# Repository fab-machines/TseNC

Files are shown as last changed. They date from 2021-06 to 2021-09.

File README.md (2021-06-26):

<div align="center"><h1 style=align="center">TseNC</h1></div>

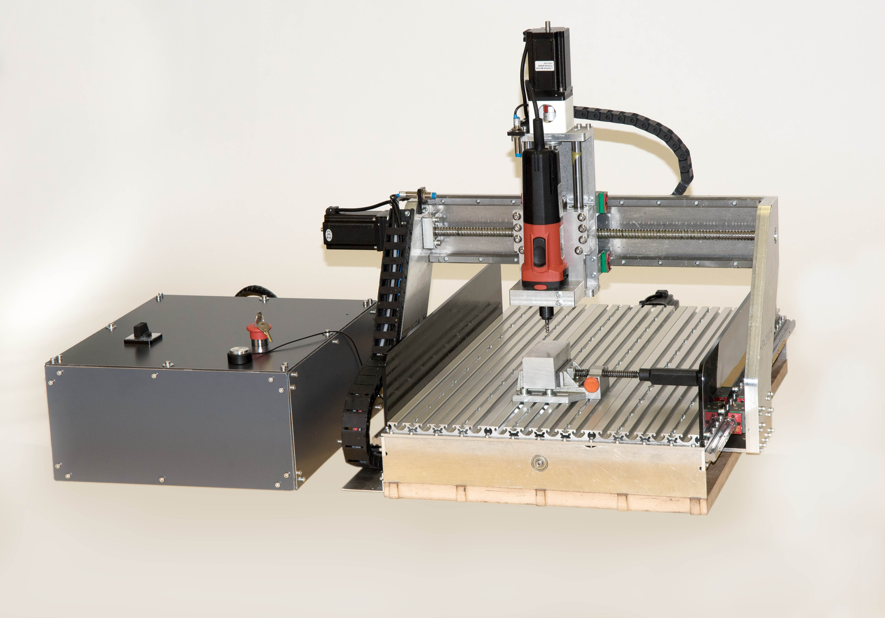
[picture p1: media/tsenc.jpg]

<div align="center"><i>Open Source CNC Milling Machine</i></div>

TseNC specifications
--

- working area: 600x370x145mm Y-X-Z (400mm on X with no side protection)
- frame: solid aluminum plates of 6/8/12/20mm bolted
- Bed: aluminum nut profiled Nut 8
- actuators: 16mm ballscrews on X and Y, 12mm ballscrew on Z
- linear guides: Hiwin HGR15
- maximum speed: 4000mm/min
- mechanical resolution: 0.003125mm
- spindle: Mafell FM1000 1Kw
- firmware: GRBL-LPC
- controller: LPC1768 32bit
- motors: NEMA 24 4MN
- motor controllers: 3 x DM556
- compatible collets: 3/4/5/6/8mm 1/8 and 1/4
- quick spindle release
- Z zero sensor
- inductive endstops with softlimits
- side procection of 6mm POM
- emergency button with fuse protection

Author
--
Project Lead:<br>
Prof. Dr. William Megill<br>
Prof. Dr. Karsten Nebe
<br>
<br>
Machine design and fabrication:<br>
Daniele Ingrassia
<br>
<br>
Technical help and assembly:<br>
Leen Nijim<br>
Kevin Brinkmann<br>
<br>
Rhine-Waal University of Applied Sciences<br>
https://www.hochschule-rhein-waal.de/en

License
--

TseNC and all the work in this repository is released under the following open source license:

CERN Open Hardware Licence - Weakly Reciprocal, CERN-OHL-W

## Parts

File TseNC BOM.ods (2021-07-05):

Name | Specifications | Amount | Unit Price (inkl. Mwst) | Total | Shipping | Vendor | Unique Vendor | Status | William | Daniele | Invoice Amt | Invoice No | Location | Total:
Linear Bearing Block | HGH15CA | 7 | €33.00 | €231.01 | 4.88 € | link (https://www.cnc-zubehoer.eu/antriebe/profilschienenfuehrungen/201/hiwin-laufwagen-hgh?c=121) | cnc-zubehoer (<=200€ netto) | Arrived | reimbursement claimed |  | €235.90 |  | Xanten (verified) | €1,793.33
Linear Bearing Block | HGH15CA | 1 | €25.00 | €25.01 |  | link (https://www.cnc-store.eu/en/bearings-blocks/bearing-block-hgh15cazac.html) | cnc-store(<=200€ netto) | Arrived | reimbursement claimed |  | €188.31 |  | Xanten (verified)
Linear Rail | HGR15RC 800mm | 2 | €40.80 | €81.98 | 8.11 € | link (https://www.cnc-store.eu/en/linear-guideways-126/guideway-hgr15-r-c.html) |  |  |  |  |  |  |  | Total netto:
Linear Rail | HGR15RC 500mm | 2 | €25.50 | €51.24 | 21.96 € |  |  |  |  |  |  |  |  | €1,545.98
Linear Bearing | LME16UU | 4 | €6.30 | €25.20 |  | link (https://www.dold-mechatronik.de/Linear-bearing-16mm-LME16UU) | dold-mechatronik (<=200€ netto) | Arrived | rechnung paid in mach |  | €224.50 | 71089 | Xanten (verified)
Linear shaft | 16mm H6 350mm | 4 | €5.10 | €20.40 |  | link (https://www.dold-mechatronik.de/Precision-shaft-16mm-h6-honed-and-hardened-300mm)
Ball Screw | 1610 800mm including nut | 1 | €90.00 | €90.00 |  | link (https://www.dold-mechatronik.de/Ball-screw-SFU1610-3-800mm)
Ball Screw | 1610 600mm including nut | 1 | €82.00 | €82.00 | 6.90 € | link (https://www.dold-mechatronik.de/Ball-screw-SFU1610-3-600mm)
Ball Screw | 1605 300mm including nut | 1 | €35.79 | €35.79 |  | link (https://gtech-shop.de/Kugelumlaufspindel-SFU1605-300mm) | GTech (<=200€ netto) |  | did this get ordered? |  |  |  |  | Missing
Coupler | D25L30 8mm to 10mm | 6 | €6.50 | €34.69 |  | link (https://gtech-shop.de/Wellenkupplung-Aluminium-flexibel-D25L30-8mm) |  | Arrived | reimbursement claimed, but needs to be switched to correct Kostenstelle |  | €101.12 |  | Xanten (verified) | They are 8 to 8mm not 8 to 10mm
Bearing | 6000ZZ | 16 | €0.80 | €10.76 |  | link (https://gtech-shop.de/Rillenkugellager-6000-ZZ) |  |  |  |  |  |  |  | cable chain are only 2
Cable Chain | Open/Closed 25x57 | 1 | €18.29 | €18.29
Cable Chain | Open/Closed 25x25 | 1 | €17.49 | €17.49 |  | link (https://gtech-shop.de/Offen-25-x-38)
Cable Chain | 30mm | 2 | €1.99 | €3.98
Cable Chain | 30mm VPE | 1 | €3.49 | €3.49
Cable Wrapper | 20mm | 2 | €1.49 | €2.98 |  | link (https://gtech-shop.de/Kabelfuehrung-Kabelbuendel-Schwarz-R20mm-25m-1-Meter)
Cable Wrapper | 10mm | 5 | €1.10 | €5.45 | 3.99 €
Aluminum Plate | 300x300x25mm CNC friendly (AlMg3, AlMgSi1 or similar) | 1 | €75.60 | €75.60 |  | link (https://www.duerr-metall.shop/p/aluminium-gussplatten-25mm-dicke-almg3-300x300mm) | DURR (<=200€ netto) | Arrived | Rechnung paid in mach |  | €189.00 | 1098 | Xanten (verified)
Aluminum Stock | 50x50x150mm CNC friendly (AlMg3, AlMgSi1 or similar) | 8 | €13.30 | €106.40 | 7.00 € | link (https://www.duerr-metall.shop/p/aluminium-vierkant-50x50mm-almgsi1-100mm)
Aluminum Plate | 800x750x6mm | 1 | €91.00 | €90.99 |  | link (https://www.ebay.de/itm/6-10mm-Aluminium-Blech-Platte-Alublech-Aluplatte-Feinblech-Zuschnitt-wahlbar/263589302349) | HLS tactical (<=200€ netto) | Arrived | reimbursement claimed |  | €90.99 |  | Xanten (verified)
Stepper motor | Nema 24 4NM 8mm shaft | 3 | €34.30 | €102.90 | 64.07 € | link (https://www.omc-stepperonline.com/nema-24-stepper-motor/dual-shaft-nema-24-stepper-motor-42a-4nm-566-ozin-60x60x100mm-4-wires-24hs39-4204d.html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) | stepperonline (<=200€ netto) | Arrived | reimbursement claimed |  | €145.84 | 56759 | Xanten (verified)
Stepper Driver | TB6600 | 3 | €12.66 | €37.98 |  | link (https://www.mechatronics-pro.de/de/stepper-motor-treiber-tb6600-4a-9-42v-controller-steuerung-cnc-schrittmotor_618.html) | mechatronics pro (<=200€ netto) | Arrived | reimbursement claimed |  | €37.98 |  | Xanten (verified)
Spindle | Mafell FM 1000 | 1 | €230.84 | €230.84 |  | link (https://www.hbh24online.de/de/-31894.html) | HBH Baumaschinenhandel GmbH (<=200€ netto) | Arrived | reimbursement claimed |  | €230.84 |  | Xanten (verified) | Collets needed!
3D Printer Filament | PETG 1KG White 1.75mm | 2 | €13.95 | €27.91 | 4.90 € | link (https://www.igo3d.com/maertz-budget-petg-filament) | igo3D (<=200€ netto) | Arrived | reimbursement claimed |  | €32.80 | 388676 | Xanten (verified)
Flat Aluminum Profile | T-Nutenplatte 600x400 16(+)mm | 1 | €118.99 | €118.99 | 15.00 € | link (https://www.ebay.de/itm/T-Nutenplatte-aus-Aluminium-fur-High-Z-S-400-T-CNC-Portalfrasmaschine/372998543104) | cnc-step (<=200€ netto) | Arrived | reimbursement claimed |  | €133.99 | 2653 | Xanten (verified)
MDF Plate | 600x800x25(+)mm | 1 | €17.90 | €17.90 | 6.90 € | link (https://www.myspiegel.de/mdf-platten-pb-4244.html) | spiegel-shop (<=200€ netto) | Arrived | reimbursement claimed |  | €24.80 |  | Xanten (verified)
Dibond | 3mm 2050x1000mm White | 1 | 37.8 | €37.80 |  | link (https://onlineshop.firstbond.de/product_info.php?no_boost=1) | firstbond (<=200€ netto) |  | donated from ENSPIRE stock |  |  |  | Xanten (verified) | alternative: | 2 plates 500x500x3mm, 4 plates 400x500 | link (https://www.ebay.de/itm/47-99-m-DIBOND-Alu-Verbundplatte-weiss-matt-3-mm-Zuschnitt-Grose-wahlbar/362029668269)
Power Plug | Power Plug With Fuse and Switch | 1 | €3.19 | €3.19 | 2.20 € | link (https://www.ebay.de/itm/Kaltgerate-C14-Einbaustecker-250-V-10-A-Schalter-Sicherungshalter-Modul-14554/293009802941) | Inetbote.de e.K. (<=200€ netto) |  | reimbursement claimed |  | €5.39 | 70843 | Xanten (verified)
Aluminum Profile | 20x20 nut 6 450mm | 36 | €0.46 | €16.56 |  | link (https://www.alu-profil-technik.de/Profil20x20-Designprofil-Aluprofile-Strebenprofile-Solarpeofile-Alubaukasten.html) | alu-profil-technik (<=200€ netto) | Arrived | reimbursement claimed |  | €58.58 |  | Xanten (verified) | Seems wrong, but should be enough for what we need!
Aluminum profiles | 20x20 Nut 6 300mm | 12 | €0.46 | €5.52
Bracket | 20x20mm nut 6 | 15 | €2.05 | €30.75 | 5.75 € | link (https://www.alu-profil-technik.de/Winkel--Verbinder--Winkel-20.html)
Wire | LIYCY 4x0.5mm 1 meter | 10 | €1.06 | €10.60 | 6.90 € | link (https://www.ebay.de/itm/Steuerleitung-geschirmt-Datenleitung-LIYCY-2-12x0-14-1-5-mm-Schnittlange-lauf-M/283736151360) | powercables-shop (<=200€ netto) |  | reimbursement claimed |  | €37.60 |  | Xanten (verified)
Wire | LIYCY 3x0.25mm 1 meter | 10 | €1.01 | €10.10
Wire | 2x1.5mm 24V | 10 | €1.00 | €10.00 |  | link (https://www.ebay.de/itm/Niedervoltkabel-2x1-5-4-mm-Niedervoltleitung-max-24-V-SIF-PV-P-laufende-Meter/272840350273)
Emergency Button | Em. Button with key | 1 | €6.00 | €5.98 |  | link (https://www.ebay.de/itm/Notausschalter-Not-aus-Schalter-Druck-Notschalter-Auschalter-Druckschalter/281817794707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) | Katarzyna Klincewicz (<=200€ netto) | Arrived | reimbursement claimed |  | €18.88 |  | Xanten (verified)
Power Switch | Power Switch 20A 2 Polig 1 Phase | 1 | €8.00 | €7.98 | 4.92 € | link (https://www.ebay.de/itm/16-160A-Nockenschalter-Drehschalter-Wendeschalter-0-1-L-0-R-0-Y-1-0-2/282083342606)
AC Cable | PC AC Power Cable | 1 | €5.40 | €5.40 |  | link (https://www.ebay.de/itm/Stromkabel-PC-Netzkabel-Kaltgeratestecker-Computer-Monitor-Drucker-Top-Zustand/124164087445) | Tech-Ced e.k (<=200€ netto) | Arrived | reimbursement claimed |  | €5.40 | 196 | Xanten (verified)
Cable connector | 12 slots, 1.5-2.5mm 5 pieces | 1 | €5.95 | €5.95 |  | link (https://www.ebay.de/itm/Lusterklemmen-12-polig-Listerklemmen-Verbindungsklemmen-1-5-16mm-Lampen-Klemme/153006846657) | Dema-Trading, Matthias Dehs (<=200€ netto) | Arrived | reimbursement claimed |  | €5.95 | 69401 | Xanten (verified)
Magnetic Switches | PS-3150 | 10 | €2.29 | €22.89 |  | link (https://www.roboter-bausatz.de/2389/ps-3150-magnetschalter-no-schliesser) | roboter bausatz(<=200€ netto) |  | reimbursement claimed |  | €22.89 |  | Xanten (verified)
Nuts | DIN 985 M4 | 100 | €0.01 | €1.07 |  | link (https://malimo24.de/Sicherungsmuttern-DIN-985-galv-verzinkt-M4-100-Stueck) | QS Vertriebs (<=200€ netto) |  | reimbursement claimed |  | €53.92 |  | Xanten (verified)
Nuts | DIN 985 M5 | 100 | €0.01 | €1.07 |  | link (https://malimo24.de/Sicherungsmuttern-DIN-985-galv-verzinkt-M5-100-Stueck)
Nuts | DIN 985 M6 | 100 | €0.01 | €1.22 |  | link (https://www.ebay.de/itm/Sicherungsmuttern-Stopmuttern-Muttern-Din-985-verzinkt/150653102538)
Nuts | DIN 985 M8 | 100 | €0.02 | €2.44 |  | link (https://malimo24.de/Sicherungsmuttern-DIN-985-galv-verzinkt-M8-50-Stueck)
Screws | DIN 912 M4 20mm | 300 | €0.02 | €4.12 |  | link (https://www.ebay.de/itm/M4-MaLiMo-DIN-912-Zylinderschrauben-galv-verzinkt-8-8/311791183620)
Screws | DIN 912 M4 30mm | 200 | €0.03 | €4.35 |  | link (https://www.ebay.de/itm/M4-MaLiMo-DIN-912-Zylinderschrauben-galv-verzinkt-8-8/311791183620)
Screws | DIN 912 M5 10mm | 100 | €0.02 | €1.32 |  | link (https://www.ebay.de/itm/M5-MaLiMo-DIN-912-Zylinderschrauben-galv-verzinkt-8-8/381944072599)
Screws | DIN 912 M5 16mm | 100 | €0.02 | €3.18 |  | link (https://www.ebay.de/itm/M5-MaLiMo-DIN-912-Zylinderschrauben-galv-verzinkt-8-8/381944072599)
Screws | DIN 912 M5 22mm | 100 | €0.02 | €3.96 |  | link (https://www.ebay.de/itm/M5-MaLiMo-DIN-912-Zylinderschrauben-galv-verzinkt-8-8/381944072599)
Screws | DIN 912 M5 30mm | 100 | €0.03 | €4.55 |  | link (https://www.ebay.de/itm/M5-MaLiMo-DIN-912-Zylinderschrauben-galv-verzinkt-8-8/381944072599)
Screws | DIN 912 M6 10mm | 100 | €0.02 | €1.93 |  | link (https://www.ebay.de/itm/M6-MaLiMo-DIN-912-Zylinderschrauben-galv-verzinkt-8-8/310573297696)
Screws | DIN 912 M6 16mm | 100 | €0.03 | €2.21 |  | link (https://www.ebay.de/itm/M6-MaLiMo-DIN-912-Zylinderschrauben-galv-verzinkt-8-8/310573297696)
Screws | DIN 912 M6 25mm | 100 | €0.03 | €2.60 |  | link (https://www.ebay.de/itm/M6-MaLiMo-DIN-912-Zylinderschrauben-galv-verzinkt-8-8/310573297696)
Screws | DIN 912 M6 30mm | 100 | €0.03 | €2.84 |  | link (https://www.ebay.de/itm/M6-MaLiMo-DIN-912-Zylinderschrauben-galv-verzinkt-8-8/310573297696)
Screws | DIN 912 M8 16mm | 100 | €0.04 | €3.57 |  | link (https://www.ebay.de/itm/M8-MaLiMo-DIN-912-Zylinderschrauben-galv-verzinkt-8-8/311791183617)
Screws | DIN 912 M8 25mm | 100 | €0.05 | €4.64 |  | link (https://www.ebay.de/itm/M8-MaLiMo-DIN-912-Zylinderschrauben-galv-verzinkt-8-8/311791183617)
Screws | DIN 912 M8 30mm | 100 | €0.04 | €3.06 |  | link (https://www.ebay.de/itm/M8-MaLiMo-DIN-912-Zylinderschrauben-galv-verzinkt-8-8/311791183617)
Washers | DIN 125 M5 | 200 | €0.01 | €1.93 |  | link (https://malimo24.de/Unterlegscheiben-DIN-125-A-Edelstahl-A2-M5-100-Stueck)
Washers | DIN 125 M6 | 200 | €0.01 | €1.93 |  | link (https://malimo24.de/Unterlegscheiben-DIN-125-A-Edelstahl-A2-M6-100-Stueck) |  |  |  |  |  |  |  | 100x M8,4 instead
Washers | DIN 125 M8 | 100 | €0.02 | €1.93 |  | link (https://malimo24.de/Unterlegscheiben-DIN-125-A-Edelstahl-A2-M8-50-Stueck)
T-Nuts | Hammermutter Nut 6 M5 | 100 | €0.15 | €17.41 | 6.72 € | link (https://www.motedis.com/shop/Nutprofil-Zubehoer/Zubehoer-20-B-Typ-Nut-6/Nutensteine-Gewindeplatten-Nut-6-B-Typ/Hammermutter-B-Typ-Nut-6-M5::7145.html) | motedis (<=200€ netto) | Arrived | reimbursement claimed |  | €24.13 |  | Xanten (verified)
 |  |  |  |  |  |  |  |  |  |  | €1,868.81
 |  |  |  |  | 1,963.53 €

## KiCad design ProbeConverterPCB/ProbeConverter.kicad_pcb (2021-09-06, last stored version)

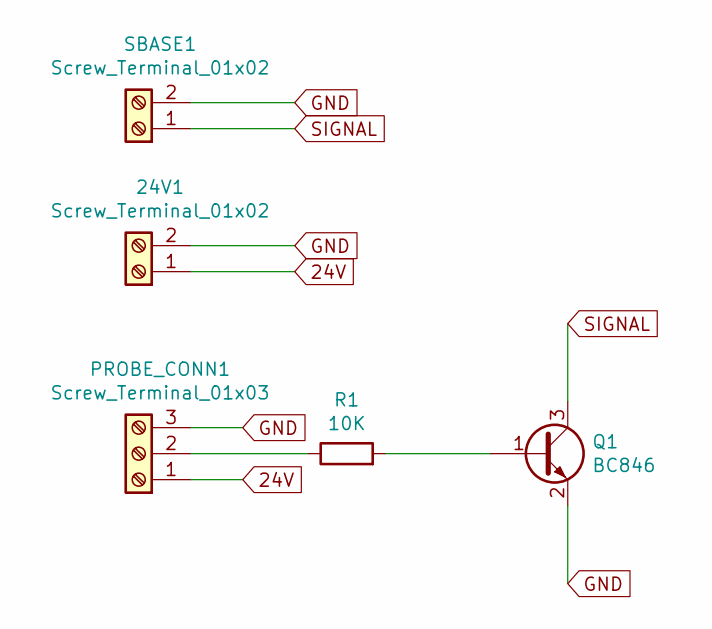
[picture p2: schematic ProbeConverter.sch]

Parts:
24V1: Screw_Terminal_01x02; TerminalBlock_bornier-2_P5.08mm
PROBE_CONN1: Screw_Terminal_01x03; TerminalBlock_bornier-3_P5.08mm
Q1: BC846; SOT-23
R1: 10K; R_1206
SBASE1: Screw_Terminal_01x02; TerminalBlock_bornier-2_P5.08mm

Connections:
24V: 24V1.1, PROBE_CONN1.1
GND: 24V1.2, PROBE_CONN1.3, Q1.2 (E), SBASE1.2
unnamed: PROBE_CONN1.2, R1.1
unnamed: Q1.1 (B), R1.2
SIGNAL: Q1.3 (C), SBASE1.1

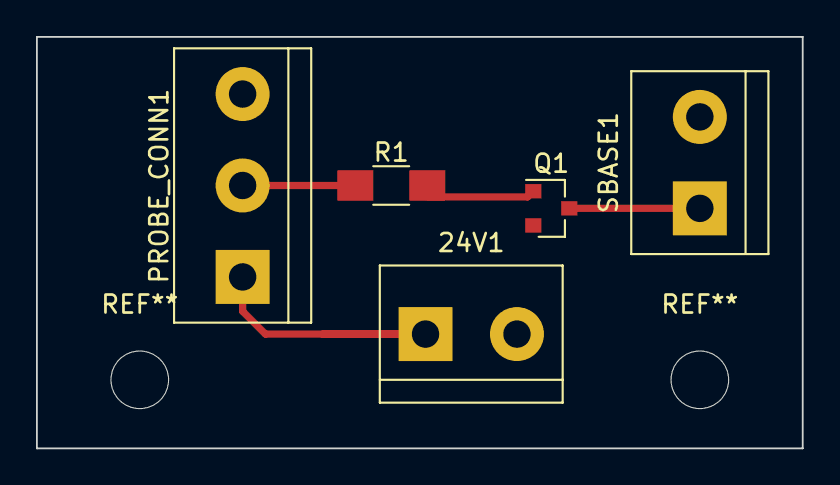
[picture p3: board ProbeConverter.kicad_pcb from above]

Board: 2 copper layers, 42.5 x 22.9 mm, 5 parts (0 on the bottom side), 5 nets.

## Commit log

2021-07-05 Add files via upload
    added initial BOM
    [TseNC BOM.ods]
2021-09-06 added probe converter pcb
    [ProbeConverter.kicad_pcb, ProbeConverter.sch]
